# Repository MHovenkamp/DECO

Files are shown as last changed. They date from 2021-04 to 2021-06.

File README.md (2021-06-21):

# DECO

## Introduction

Welcome to the Github page for the social robot under 50 euros. This robot is the result of a student project by the name PINNO, personal innovation project. This robot is to be possibly used by the minor social robotics from Hogeschool Utrecht.

## What can the robot do?

DECO is a desk companion for people with a desk job. The robot reminds the user to stay healthy and productive without being pushy. The robot reminds people to take breaks and drink enough water. It can also inform the user of their current environment such as temperature. These are al possibilities within the robot but the goal is that this robot can easily be programmed by someone with limited knowledge of technology. THis is so the robot can be used by the previously mentioned minor from the HU.

## Printing the robot
Each part of the robot can be printed separated or if you have a bigger printer, be placed in one STL. Before you print you do have to add supports. This can be done easily with Ultimaker Cura.

## building the robot

The head:
The head consists of two parts: a roundish ball, the lower head and a dome for the face. 
1. Place the micro lidar and the oledscreen in the upper face and make sure that they are stuck using either a little bit of glue or some electricity tape.
2. place on of the servo motors in the g0 degree position, THsi can be done by connecting to the Arduino and running the return_to_start_pos command. Glue the neck horizontal to the servo motor making sure that there is a 90 degree angle between the motor and the neck.
3. place the servo with the neck part in the slot in the lower body and attach with some glue. 
4. Route all the cables for the components through the whole in the bottom of the lower body

The body:
1. Stick the servo through the bottom hole of the upper body. And turn the servo to 90 degrees. glue the vertical neck part to the servo with the attachment part diagonal to the servo. 
2. Attach the PIR sensor through the whole and attach with taper or glue. place the arduino in the bottom lower body and connect al the cables as shown in the Fritzing. 

Attachment
Connect the upper head to the lower head with some glue making sure the head looks up and down if the servo is moved. 
Slide the two neck pieces to each other attaching the robot together, make sure al the wires can get to the arduino with some space for movement. glue the lower and upper body together after connecting the usb cable into the arduino making sure the PIR sensor looks forward.

Voila! Robot. 

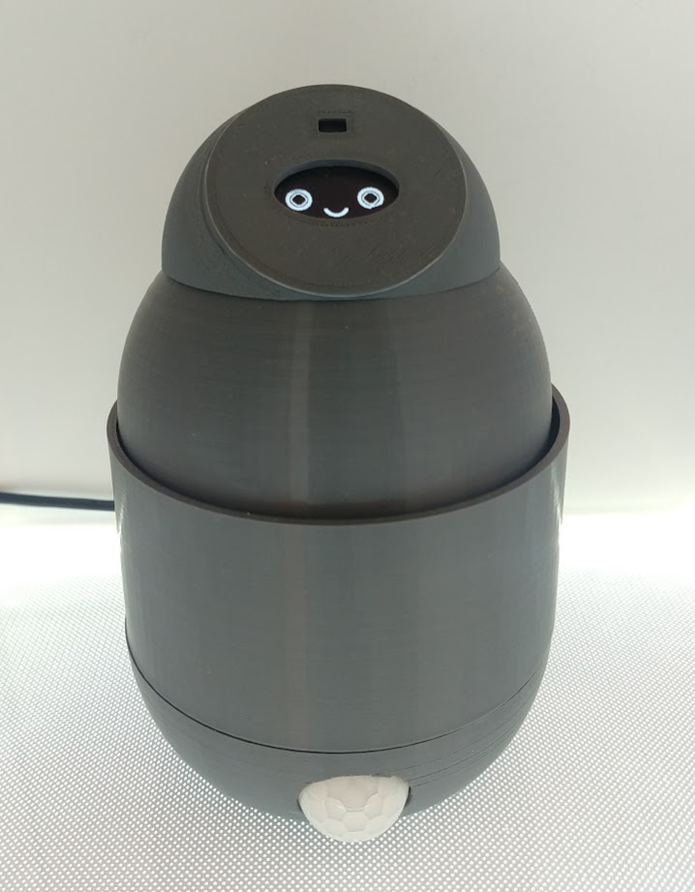
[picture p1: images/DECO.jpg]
DECO


## Necessary components to build this robot.

1. 3D printer
2. 2 * SG90 or SG92R servo motors, These both work the same but the SG92R ia a little stronger. 
    - [Amazon](https://www.amazon.nl/AZDelivery-Micro-Helikopter-Vliegtuigen-Inclusief/dp/B07CZ42862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)
3. Arduino nano 33 BLE SENSE
    - [Arduino store](https://store.arduino.cc/arduino-nano-33-ble-sense)
4. PIR sensor HC-SR501
    - [Amazon](https://www.amazon.nl/AZDelivery-HC-SR501-Detection-compatibel-Inclusief/dp/B07V6BY66P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)
5. OLED 0.96 display
    - [Amazon](https://www.amazon.nl/Jolicobo-OLED-weergavemodule-kijkhoek-doe-het-zelf-projectdisplay/dp/B07RNP3CMP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)
6. Piezo buzzer
    - [Amazon](https://www.amazon.nl/GLOGLOW-elektronische-zoemer-actieve-geluid/dp/B07F5LB8K9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)
6. Cables
    - Male to female 
    - female to female
7. Arduino compatible USB cable.
    - [Arduino store](https://store.arduino.cc/usb-cable-type-a-male-to-micro-type-b-male)
8. Soldering iron and necessary accessories.

total cost from amazon +- 63,18, You can probably get cheaper components from your local stores.  

## Documentation
For documentation run this command in the github directory
```
doxygen Doxyfile
```

## Models

### Fritzing
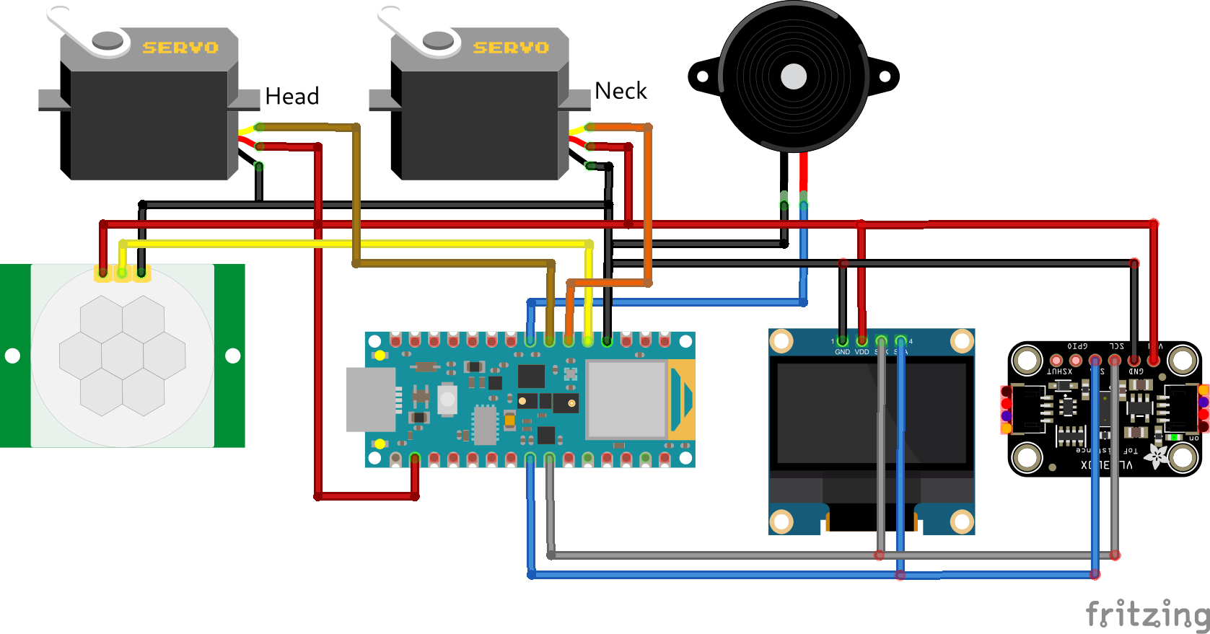
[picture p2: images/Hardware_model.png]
Fritzing Model


Al other models can be found by opening software_models.html.

## Building and running
This robot is compiled and flashed by [PlatformIO](https://platformio.org/). Install platformIO core to work with this project. Then run the following commands in a terminal in the directory. The directory will build the robot and flash to your arduino. PlatformIO will install all libraries and updates by itself. If something does not work try updating the libraries through platformIO trough the commando 
```
platformio update
```

To run: 
```
platformio run -t upload
```
If the right port cant be found change port to correct port with this command:
``` 
platformio run -t upload --upload-port <port>
```
You can find the correct port with:
```
pio device list
```
After flashing the robot will instantly start working. If the robot loses power and is then reconnected it will restart the program.

To open a serial monitor to the robot use the command:
```
pio device monitor
```

## Code layout
To write the preprogrammed code or to upload a file the code given has to be in a certain structure:

The setup wil run once and can be used to place som e setters before you start your program. The loop section will do exactly that: loop until the robot dies or power is removed.

```
SETUP:

// setup code

LOOP:

// code that will be looped

EOF:
// define end of code file

```

## command line interface
The command line interface has 3 ways to start code with.
1. REPL
2. FILE
3. PREPROGRAMMED FILE

### REPL 
You can enter a single command in here to see the result instantly. You can not test with integers since they are not saved from previous commands
### FILE
Ctrl+C plus Ctrl+V a full file in to the terminal to instantly parse and run the code. Warning: The serial buffer for arduino is famously unreliable so bigger files will most likely be read wrong. For files bigger then 10 lines of code use the PREPROGRAMMED FILE function.
### PREPROGRAMMED FILE
Start the preprogrammed file found in the programCode.cpp file. You have to recompile the robot every time you change this file. This file will also be played if no serial monitor is started.

## Commands:

### Instant commando's
- ```shutdown```, The robot shuts down until movement is detected.
- ```interactive_mode```, The robot tries to follow an object in front of its face but looses interest if no object is found.
- ```break_reminder```, Show the break reminder on the screen for the set duration. 
- ```walk_reminder```, Show the walk reminder on the screen for the set duration.
- ```water_reminder```. Show the water reminder on the screen for the set duration.
- ```show_weather_station```,show the weatherstation on the screen for the set duration. NOTE: The temperatures, BARO and humidity are measured inside the robot and can be inaccurate. 
- ```rng_movement```, move the robot once to a random position.
- ```return_to_start_pos```, Return the robot to the start position of 90 by 90 degrees. 
- ```move_head x```, move the head to x degrees. 40 <= x => 140
- ```move_neck x```, move the neck to x degrees. 0 <= x => 180.
- ```playSound x``` play start up sound. x:
    -   start_up
    -   shut_down
    -   notification
- ```WAIT x y```. x: Integer, y: cannot be an integer variable
    -   define HOUR 
    -   MINUTE 
    -   SECOND 
    -   MIllI_SECOND 

### IF conditions
You can maken if statement using some of the getters describe in the next paragraph. You can not place one if statement in another if statement. 
```
IF(getState = IDLE){
    // Code to execute if statement is true.
}
```
Possible commands:
-   getDistance >/</<=/>=/==/!= int
-   getState == STATE
-   getHeadPos >/</<=/>=/==/!= int
-   getNeckPos >/</<=/>=/==/!= int
-   getLastMovementDetected >/</<=/>=/==/!= int

you can use an int variable for every int mentioned above.

### WHILE loops
You can make a small part of your code loop for as long as a given condition is true
```
WHILE(getState = IDLE){
    // Code to loop execute if statement is true.
}
```
possible conditions1
-   x : X can be any number, The loop wil continue for x iterations.
-   getDistance >/</<=/>=/==/!= int
-   getState == STATE
-   getHeadPos >/</<=/>=/==/!= int
-   getNeckPos >/</<=/>=/==/!= int
-   getLastMovementDetected >/</<=/>=/==/!= int
IMPORTANT: if you change the value of an integer value used in the condition this change will not affect the x used in the condition. You can not use getHeadPos > x and then change x in the while loop to shorten or lengthen the loop. 

### Integers and math
The code for this robot contains a small amount of possible math. You can assign a number to a variable like this:
```
x = 6
variable = 6
variable_number = 6
```
You can add, subtract, divide and multiply with integers. You can only change existing integers.
```
SETUP:
    x = 2
    y = 3
    x + y # result = 5

    x = 2
    y = 3
    x - y # result = -1

    x = 2
    y = 3
    x * y # result = 6

    x = 6
    y = 3
    x / y # result = 2
EOF:
```
You can use numbers for the right side of any math operator
```
SETUP:
    x = 2
    x + 3  # result = 5

    x = 2
    x - 3 # result = -1

    x = 2
    x * 3 # result = 6

    x = 6
    x / 3 # result = 2
EOF:
```
limitations
You can not assign the output of a function to an integer variable.

### Getters
- ```getDistance```, Get the distance currently measured by head lidat
- ```getBreakTime```, Get the duration of the break time reminder.
- ```getWalkTime```. Get the duration of the walk time reminder.
- ```getWaterTime```, Get the duration of the water time reminder.
- ```getWeatherStationTime```, Get the duration of the weather station.
- ```getState```, get the current state of the robot:
    -   IDLE,
    -   REMINDER_BREAK
    -   REMINDER_WATER
    -   REMINDER_WALK
    -   WEATHER_STATION
    -   INTERACTIVE_MODE
    -   OFF
-   ```getHeadPos```, get the current position of the head in degrees with 90 being straight forward.
-   ```getNeckPos```, get the current position of the neck in degrees with 90 being straight forward.

### Setters
Set if timed functions are active or not:
- ```weatherstation = x```:
    -   ACTIVE
    -   NON_ACTIVE
- ```walk_reminder = x```:
    -   ACTIVE
    -   NON_ACTIVE
- ```weatherstation = x```:
    -   ACTIVE
    -   NON_ACTIVE
- ```break_reminder = x```:
    -   ACTIVE
    -   NON_ACTIVE
Set the state of the robot
- ```STATE = x```:
    -   IDLE,
    -   REMINDER_BREAK
    -   REMINDER_WATER
    -   REMINDER_WALK
    -   WEATHER_STATION
    -   INTERACTIVE_MODE
    -   OFF
Set the time duration after which the robot will shut down if there is no movement.
- ```shut_down_after = x y```: x = integer, y = 
    -   HOUR 
    -   MINUTE 
    -   SECOND 
    -   MIllI_SECOND 
set the duration and the period of a timed event.
a :
-   weatherstation
-   walk_reminder
-   water_reminder
-   break_reminder
- ```a DURATION = x y```: x = integer, y = 
    -   HOUR 
    -   MINUTE 
    -   SECOND 
    -   MIllI_SECOND 
- ```a PERIOD = 10 MINUTE```: x = integer, y = 
    -   HOUR 
    -   MINUTE 
    -   SECOND 
    -   MIllI_SECOND 
set how long the robot i allowed to follow an object in interactive mode.
- ```interactive_mode DURATION = x y```: x = integer, y = 
    -   HOUR 
    -   MINUTE 
    -   SECOND 
    -   MIllI_SECOND 

## License 

DECO
Copyright (C) <year>  <name of author>

This program is free software: you can redistribute it and/or modify
it under the terms of the GNU General Public License as published by
the Free Software Foundation, either version 3 of the License, or
(at your option) any later version.

This program is distributed in the hope that it will be useful,
but WITHOUT ANY WARRANTY; without even the implied warranty of
MERCHANTABILITY or FITNESS FOR A PARTICULAR PURPOSE.  See the
GNU General Public License for more details.

You should have received a copy of the GNU General Public License
along with this program.  If not, see <https://www.gnu.org/licenses/>.

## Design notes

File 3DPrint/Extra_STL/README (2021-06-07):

Some people had issues printing the upper body of the robot. Therefore two new STL files have been made to make it possible to print the upperbody in two seperate pieces. The upper body can now be connected to the middle body to form the original upper body.

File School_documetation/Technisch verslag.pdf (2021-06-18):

## Maaike Hovenkamp

1741256

# DECO Technisch verslag

18-06-2021

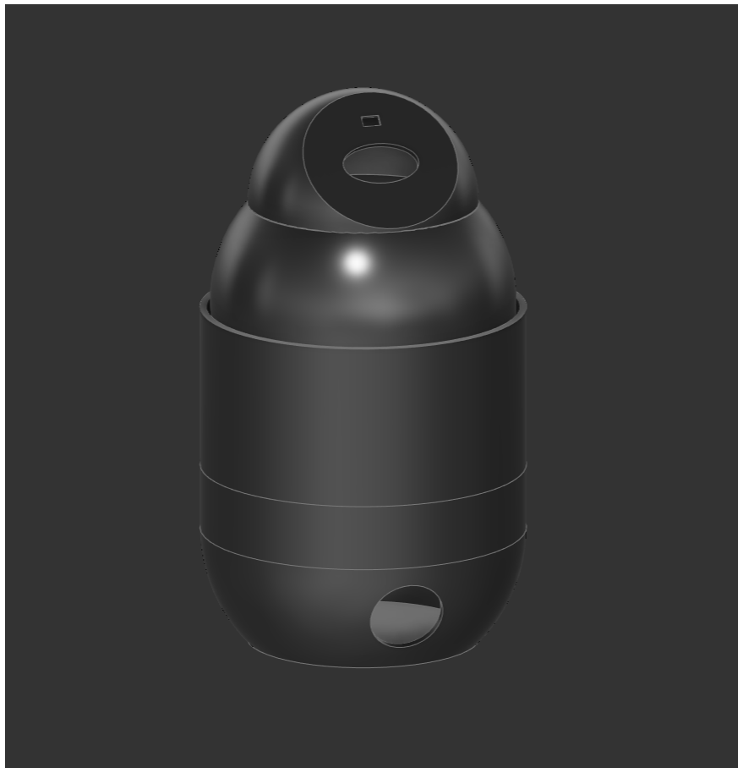
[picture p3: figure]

Inleiding | 2
Microcontroller | 2
Ontwikkelings taal | 2
Python | 3
C++ | 3
Ontwikkelingsomgeving | 3
Resultaten software | 4
Externe hardware | 4
Servomotoren | 4
Externe Sensoren | 4
Display | 4
Bronnen | 5

## Inleiding

Dit is het technisch verslag voor de DECO robot, er wordt ingegaan op de specifieke gekozen hardware en ontwikkel omgeving. Er wordt niet ingegaan op het fysieke ontwerp van de robot aangezien dit is opgenomen in het Design verslag.

## Microcontroller

Het hart van de robot is de microcontroller die het hele systeem laat werken. Voor deze robot is er gekozen voor de Arduino nano 33 BLE SENSE. Deze arduino is gekozen voor zijn snelheid en kleine vorm.

De arduino nano is een microcontroller van het merk Arduino en werkt op een nRF52840 processor van Nordic Semiconductors. Deze microcontroller heeft meer geheugen en ram dan de grotere arduino Uno. waardoor er grotere programma’s kunnen worden geschreven.

De nano 33 ble sense is een uitbreiding op de arduino nano 33 ble en komt met extra sensoren die gebruikt kunnen worden om kennis van de omgeving te verzamelen.

## Ontwikkelings taal

De gekozen microcontroller is een relatief nieuwe microcontroller, 2019, waardoor er bepaalde limieten zijn in keuze van ontwikkelings talen. Er zijn twee taal mogelijkheden voor deze microcontroller: een vorm van Python en C++.

## Python

Python is een redelijk toegankelijke taal voor de beginnende programmeur waardoor gebruikers op een dieper niveau met de robot kunnen werken. Python zelf werkt niet op microcontrollers maar er zijn aanpassingen op python gemaakt zodat het bruikbaar is op een microcontroller. Circuitpython van Adafruit is er hier een van. Het is een verdere uitbouw op MicroPython. Circuitpython heeft een eigen bootloader die eerst op de arduino moet worden geïnstalleerd. Momenteel is er geen Circuit Python implementatie voor de arduino nano 33 ble sense maar wel voor zijn lite versie de arduino nano 33 ble. Deze lite versie heeft minder sensoren dan de arduino nano 33 ble sense waardoor veel sensoren van de arduino nano 33 ble sense niet ondersteund worden door circuit python. De sensoren op de arduino nano 33 ble sense hebben zelf libraries van circuit python maar hier wordt gewerkt met externe sensoren. Een voordeel van circuit python is de geïntegreerde REPL waardoor code snel kan worden getest. Dit heeft een voordeel voor de gebruiker als deze gebruiker niet bekend is met het schrijven van code.

C++

De makers van de arduino nano 33 ble sense maken zelf ook de libraries en andere support voor hun producten. Deze libraries zijn geschreven en bedoeld voor de taal C++. C++ is een moeilijkere taal dan python gefocust op snelheid. Aangezien de makers van de arduino zelf hun libraries maken is er volledige support voor de arduino nano 33 ble sense. Er zijn libraries ontwikkeld voor alle sensoren en deze worden ook regelmatig geupdate. Een belangrijk punt van C++ en arduino is dat alle code op de laptop gecompileerd wordt voordat het naar de arduino wordt gestuurd. Dit zorgt ervoor dat alle code moet bestaan voordat de gebruiker kan testen en heeft een bepaalde wachttijd.

Er is voor dit project gekozen om en de taal C++ te werken aangezien de support van de makers betrouwbaar en constant is. Dit zorgt er wel voor dat er voor de user interface mogelijk niet met REPL kan werken. Dit zou betekenen dat er een langere wachttijd is voor de gebruiker.

## Ontwikkelingsomgeving

Met de keuze voor C++ zijn er ook een aantal mogelijke ontwikkelomgevingen geopend. Arduino heeft een standaard ontwikkelomgeving waar code geschreven, gecompileerd en geflashed kan worden. Het nadeel van deze omgeving is dat er weinig debug opties zijn en dat er geen bestanden naast elkaar open kunnen worden gezet. Zelf heb ik een voorkeur voor visual studio code door zijn vele debug opties en nette interface. Er is de mogelijkheid op de arduino IDE bestanden te openen en te bewerken met visual studio code maar ze zouden alsnog met de arduino IDE gecompileerd en geflashed moeten worden. Om deze redenen ben ik overgestapt op Platformio. PlatformIO is een een cross platform visual studio code extensie waarmee code voor microcontrollers kan worden geschreven in C++ met alle arduino libraries (PlatformIO labs, n.d.). Alle code wordt geschreven, gecompileerd en geflashed met behulp van PlatformIO zonder dat de arduino IDE gebruikt wordt. Om alleen code te compileren en te flashen is er ook cross platform command line support.

## Resultaten software

De uiteindelijke keuzes voor dit project zijn:

Het DECO project wordt in de taal C++ geschreven voor de arduino nano 33 ble sense en gecompileerd een geflashed door PlatformIO.

## Externe hardware

Om ervoor te zorgen dat de robot met zijn omgeving kan interacteren wordt er gebruik gemaakt van externe hardware.

## Servomotoren

Om de robot te laten bewegen zijn er twee servomotoren aan het ontwerp toegevoegd. Er is gekozen voor de sg92R. Dit is een kleine compacte servomotor met genoeg kracht om de robot te laten bewegen zonder een externe voedingsbron te hebben (ServoDatabase, n.d.).

## Externe Sensoren

De robot heeft buiten de microcontroller ook een paar externe sensoren. Een van deze sensoren is een Passive Infrared sensor, PIR, DIe opmerkt of er beweging in de ruimte is. DIt wordt gebruikt om te testen of de robot niet alleen in een ruimte is. De HC-sr501 is een adequate sensor voor deze situatie met een degelijk bereik (MPJA, n.d.). Om een persoon te detecteren binnen een ruimte maakt de robot gebruik van een tweede sensor geplaatst in het hoofd. Dit is de sensor vl53l0x. Deze kleine afstand sensor is goed te verwerken in het ontwerp is precies genoeg. (Tinytronics, n.d.)

## Display

Er wordt gebruikgemaakt van een zwart wit I2C display ter grootte van 128*64 pixels. Dit is een kleine maar efficiënte display met een laag stroomverbruik (Adafruit).

## Bronnen

Adafruit. (2008, April). SSD1306 Datasheet. cdn-shop.adafruit.com. Retrieved 6 15, 2021, from

https://cdn-shop.adafruit.com/datasheets/SSD1306.pdf

MPJA. (n.d.). HC-sr501 datasheet. MPJA. https://www.mpja.com/download/31227sc.pdf

PlatformIO labs. (n.d.). PlatformIO. platformio.org. Retrieved 6 16, 2021, from https://platformio.org/

ServoDatabase. (n.d.). SG92R datasheet. ServoDatabase.com.

https://servodatabase.com/servo/towerpro/sg92r

Tinytronics. (n.d.). Tinytronics, datasheet link. TinyTronics.

https://www.tinytronics.nl/shop/nl/sensoren/afstand/vl53l0x-time-of-flight-tof-afstandsenso

r

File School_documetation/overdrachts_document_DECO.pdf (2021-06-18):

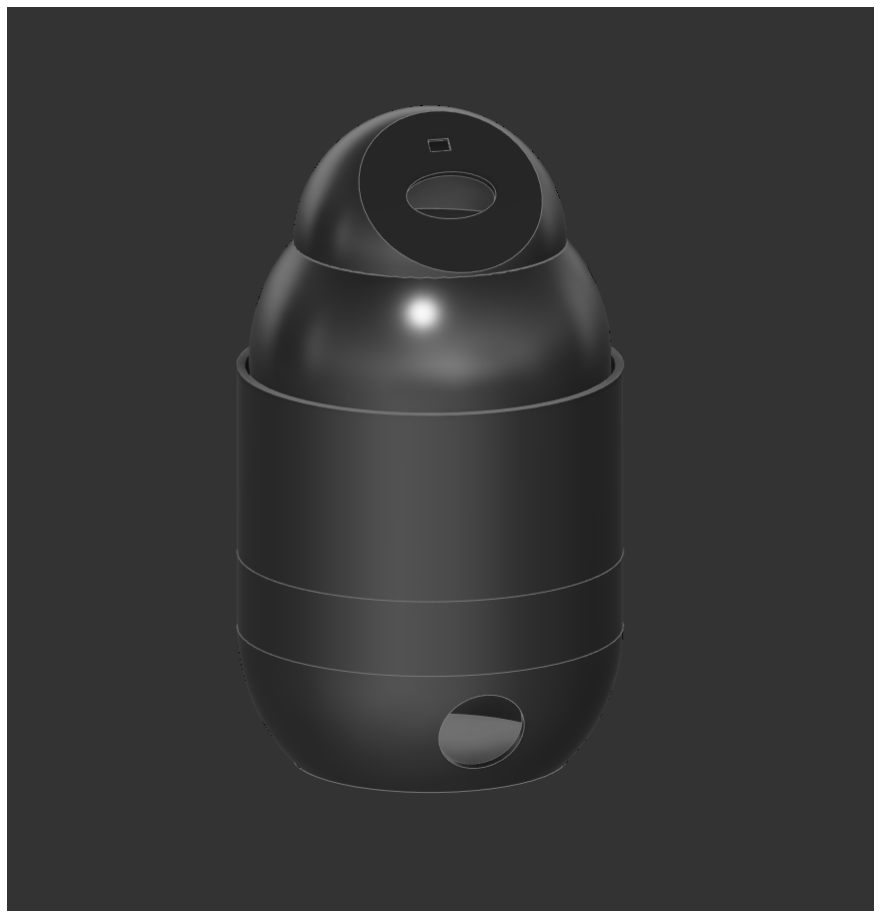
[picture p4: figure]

# Overdrachtsdocument DECO

18-06-2021
─

## Maaike Hovenkamp

### Personal innovation 2021

## Inleiding

Welkom bij de inleiding voor het overdrachtsdocument voor de sociale desktop companion DECO. DECO is een makkelijk programmeerbare robot voor op je bureau om je gezelschap te houden door de dag heen. DECO kan gebruikt worden om je te herinneren voor jezelf te zorgen door de dag heen en je te vermaken met een klein spelletje. Om ervoor te zorgen dat de robot makkelijk toegankelijk is, is er gekozen voor goedkopere onderdelen. Met amazon komt het totaal uit op +- 64 dollar maar lokale bronnen hebben vaak goedkopere onderdelen.
DECO is volledig ontworpen en geproduceerd door Maaike Hovenkamp.
Inleiding | 1
Artefacten | 1
STL files voor DECO | 1
Software | 2
Software & hardware modellen | 2
Documentatie | 2
Bugs en beperkingen | 3
Bugs | 3
Beperkingen | 3
Product backlog | 3

## Artefacten

Alle documentatie is te vinden op de Github pagina: https://github.com/MHovenkamp/DECO

## STL files voor DECO

Om de robot te printen zijn zes STL files geproduceerd:
1. Neck horizontal part, Deel 1 van neck gedeelte.
2. Neck vertical part, Deel 2 van neck gedeelte.
3. Lower body, voet van de robot met gat voor voeding en PIR-sensor
4. Upper body, Verlengstuk voor de voet met kom voor hoofd.
5. Lower head, bodem van hoofd passend in de kom van het lichaam.

6. upper head, Hoofd met gat voor OLED-screen en LIDAR module.

Er is een extra set aan STL file voor de upper body waarin dit onderdeel in 2 stukken is gesneden.

## Software

Om de robot te besturen is er code geschreven in C++ op het framework van PlatformIO. PlatformIO is een cross-platform embedded development platform integreerbaar in visual studio code. De robot maakt gebruik van een paar libraries:
1. Adafruit BusIO, Oled screen
2. Adafruit GFX Library, Oled screen
3. Adafruit SSD1306, Oled screen
4. Adafruit_VL53L0X, LIDAR
5. Arduino_HTS221, interne luchtvochtigheid en temperatuur
6. Arduino_LPS22HB, interne BARO sensor
Om met de software te werken moet PlatformIO geïnstalleerd worden en de github pagina als project ingeladen worden. Alle libraries en build platformen worden automatisch geïnstalleerd bij de eerste build.

## Software & hardware modellen

Voor de software zijn modellen gemaakt volgens de UML methode:
1. Object model
2. Task scheduling
3. Class diagram
4. State transition diagrams.
Er is een fritzing voor de kabel layout.
Deze bestanden zijn te vinden op de Github pagina.

## Documentatie

Voor de DECO robot zijn verschillende verslagen geschreven.
1. Design document, Een overzicht van alle design keuzes en de daaruit volgende Use cases. In dit verslag zijn de keuzes voor hardware en software niet vastgelegd.
2. Technische verslag, In dit verslag wordt er een onderbouwde keuze gemaakt voor:
a. Code taal
b. Ontwikkelomgeving
c. Hardware

## Bugs en beperkingen

Na vier maanden werken aan de DECO robot zijn de volgende bugs en beperkingen aanwezig:

### Bugs

- De robot heeft momenteel een probleem met een tikkend geluid over de I2C bus. Een tik is hoorbaar.
- De robot verliest af en toe de functionaliteit over de servo motoren. Na de een keer de kabels te hebben bewogen werkt de robot weer. De kans dat het een slechte kabel is bestaat maar het kan ook een probleem zijn met de stroomlevering. Het probleem wordt significant minder als de servomotoren geen ground meer delen met het Oled scherm.
- De serial input van Arduino is niet extreem betrouwbaar waardoor file input vanaf de terminal na een bepaalde grootte niet meer succesvol werkt.

### Beperkingen

- De robot heeft momenteel 6 threads lopen waardoor een getimede task later kan zijn. Een interpreter commando kan een seconde achterlopen. Alle sensoren worden wel correct getimed.
- De codetaal is momenteel erg beperkt. Momenteel worden een aantal robot commandos ondersteunt en een hele minimale interpreter met integer support, if nodes en while nodes. Alles wordt geparsed en gelexed maar er kunnen meer specifieke errors worden toegevoegd en betrouwbaarheid kan hoger. DIt kan gedaan worden door bijvoorbeeld elk commando met een ; af te sluiten en hier op te parsen.

## Product backlog

Hierbij de originele use cases, een volledig overzicht is te vinden in het design document.
1. Als gebruiker wil ik dat de robot mensen herinnert om elk half uur minimaal vijf minuten te bewegen.
2. Als gebruiker wil ik dat de robot mensen herinnert om elke twee uur een pauze te nemen.
3. Als gebruiker wil ik dat de robot mensen herinnert om elk uur een glas water te drinken.
4. Als gebruiker wil ik dat de robot een uitknop heeft waar de robot mee uitgeschakeld kan worden.

5. Als gebruiker wil ik dat de robot gebruik maakt van piepjes, beweging en afbeeldingen om te communiceren.
6. Als gebruiker wil ik dat de robot heeft een scherm waarop instructies kunnen worden getoond.
7. Als gebruiker wil ik dat alle documentatie rond het gebruik van de robot in engels wordt geschreven.
8. Als gebruiker wil ik dat de robot op een standaard USB-poort kan worden aangesloten voor stroom.
9. Als gebruiker wil ik dat de robot geen gegevens deelt met derde partijen.
10. Als gebruiker wil ik dat de robot geen gegevens over de gebruiker verzamelt afgezien van wat de gebruiker de robot geeft.
11. Als gebruiker wil ik dat de robot geen scherpe randen of puntige objecten heeft.
12. Als gebruiker wil ik dat de robot stationair is en niet zonder de hulp kan verplaatsen.
13. Als gebruiker wil ik dat de robot de vooraf geplande acties uitvoert en hier niet van afwijkt.

De enige use case die niet uitgewerkt is een mogelijke uitknop voor de robot.
De originele backlog voor dit ontwerp is grotendeels afgerond maar ik wil in dit kopje wat verdere inspiratie geven voor mogelijke toekomstplannen voor DECO.
Verdere interpreter mogelijkheden:
1. Toevoegen van een printfunctie voor debuggen. Outputen van integer waarden en string variabelen.
2. Output van functies opvangen in integer nodes en hiermee kunnen rekenen.
3. Implementeren van bolean waardes, momenteel kunnen integer nodes hiervoor gebruikt worden maar een individuele variabele soort kan gewaardeerd worden. Robot mogelijkheden
1. Meer vormen van interactie met de gebruiker, denk aan meer vormen van geluid.
2. De microcontroller van de robot kan een klein tensorflow model ondersteunen, De robot kan meer sociaal worden als hij zelf meer keuzes kan maken. Met een klein neuraal netwerk zouden meer natuurlijke keuzes kunnen worden gemaakt.

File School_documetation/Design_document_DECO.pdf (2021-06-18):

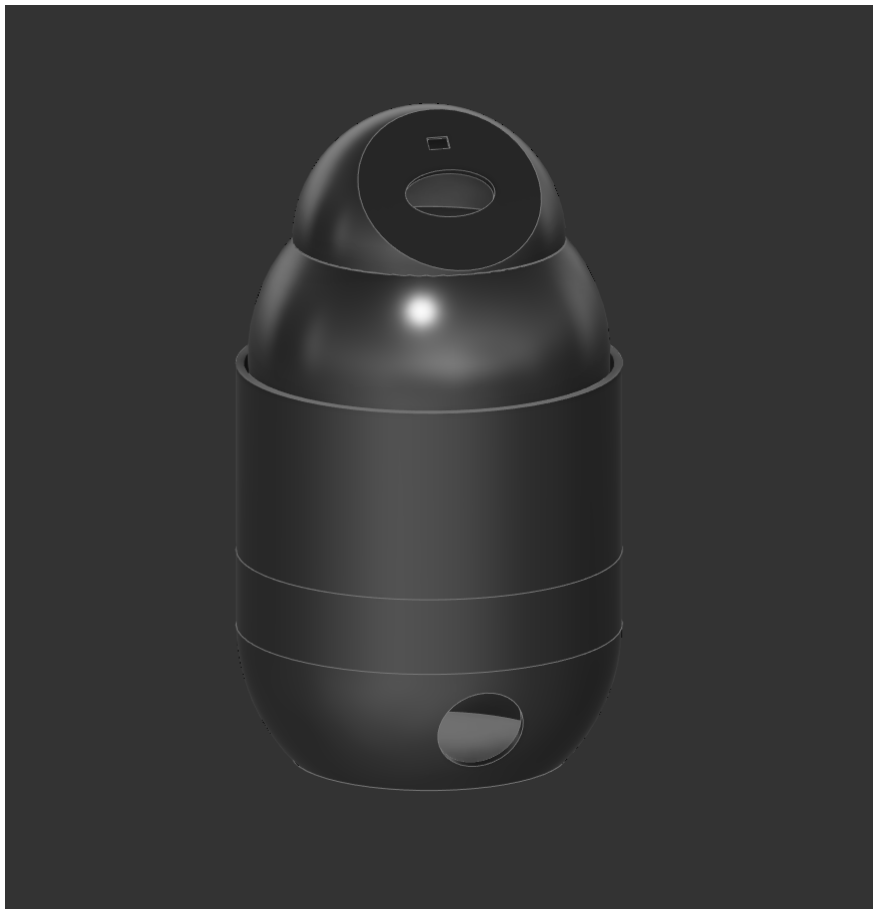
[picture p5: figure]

# Design document DECO

18-6-2021

## Maaike Hovenkamp

### Personal Innovation Hogeschool Utrecht

1741256

## Overzicht

Dit is het ontwerp document voor het Personal Innovation project van Maaike Hovenkamp. In dit document ga ik mijn ontwerpprocess uitwerken en uitleggen.

Als eerste ga ik over een paar verschillende bestaande robots om te kijken of deze robots sociaal zijn en om te kijken of ik deze robots als basis kan gebruiken voor mijn robot. Hierna ga ik op deze robot verderwerken met onderstaande methoden of begin ik een volledig nieuw ontwerpprocess.

Ik ga verschillende methoden van de minors “Design methods for robots” en “Human robot interaction” toepassen. Met deze methoden hoop ik een goed ontwerp te maken om daarmee een succesvolle sociale robot te maken.

Het doel van mijn sociale robot wordt om een desk companion te zijn en om lange werkdagen leuker te maken. De robot kan op een bureau geplaats worden en zorgd voor interactie met de gebruiker wat eenzaamheid verminderd. De robot zal ook een paar nuttige functies krijgen om de gebruiker te helpen bij self care. Deze functies zullen uit een value sensitive design process komen.

Als er een robot ontwerp gemaakt is zal ik de robot naast een framework leggen om te kijken of de robot als “sociaal” kan worden beschreven. Dit framework is gemaakt door Christoph Bartneck en Jodi Forlizzi (Bartneck & Forlizzi, 2004, 591-594).

In dit bestand worden een aantal termen gebruikt uit de twee vakken van de minor Social Robotics. Veel van deze termen worden gebruikt in opsommingen. Als de betekenis van de termen voor de lezer belangrijk is zullen deze worden uitgelegd. Als de termen niet uitgelegd zijn betekent dit dat er niet van de lezer verwacht wordt deze termen te begrijpen en staan zij erin voor tekst compleetheid.

Overzicht | 2
Bestaande robots | 4
Keuze fysieke ontwerprichting | 5
Value sensitive design | 6
Stap 1, Value discovery | 6
Directe stakeholders | 6
Indirecte stakeholders | 6
resultaten | 6
Stap 2, Value conceptualization | 8
Human welfare | 9
Privacy | 9
Universal usability | 10
Trust | 10
Autonomy | 11
Stap 3, Empirical value investigation & Stap 4, Technical value investigation | 11
Human welfare | 12
Privacy | 12
Universal usability | 13
Trust | 13
Autonomy | 14
Use cases | 15
MoSCoW | 21
Robot ontwerp | 21
Gezicht animaties | 23
Robot naamgeving | 25
Bronnen | 25

## Bestaande robots

Er is gekeken naar 11 verschillende robots om te kijken of dit een robot is om verder op te ontwikkelen of om als inspiratie te nemen. De onderzochte robots zijn:

❏ Buddy
❏ Tito
❏ The emotion robot
❏ littlebot
❏ peeqo

❏ vector
❏ pia
❏ pico
❏ emo

Deze robots zijn beoordeeld op hoe sociaal ze zijn met het framework van Christoph Bartneck en Jodi Forlizzi (Bartneck & Forlizzi, 2004, 591-594). Binnen dit framework krijgen robots een score op 5 verschillende gebieden:

- Form, Is de robot abstract, biomorphic or anthropomorphic? verdere uitleg in volgend kopje.
- Modality, Is de robot unimodal or multimodal? heeft de robot meerdere vormen van interactie: zoals beweging en geluid.
- Social norms, Heeft de robot begrip van sociale normen?
- Autonomy, Beslist de robot zelf welke acties worden uitgevoerd?
- Interactivity, Is er de mogelijkheid om met de robot te interacteren?

Op basis van dit framework heb ik de robots een sociale score gegeven om ze te kunnen ordenen. Ik heb opgeschreven welke design keuzes ik zou willen meenemen van de robots en of ik de robots zou kunnen reproduceren in de tijd voor dit project, 2 schoolblokken +- 4 maanden. Hieronder een overzicht van elke score. De bronnen van de robots kunnen aan het eind van dit bestand gevonden worden.

naam robot | Sociale score 1/10 | mogelijkheid om te maken | Wat wil ik meenemen uit dit design
Buddy | 5 | ja | De Buddy robot is een goed na te maken robot en heeft veel ruimte voor verbetering. Ik vind de beweging van de nek interessant en neem dit waarschijnlijk mee naar mijn eigen ontwerp.
Tito | 3 | ja | De Tito robot heeft niet veel wat ik mee zou willen nemen. Misschien de interactie van het dansen.
The emotion robot | 1 | nee | Het design is schattig en ik wil het scherm gezicht idee overnemen in mijn eigen ontwerp.

Littlebot | 2 | nee | Van de Littlebot wil ik niet iets meenemen.
Vector | 9 | nee | Van de Vector wil ik de nuttige functies overnemen zoals een mogelijk weerstation of een herinnering om wat te drinken en een rondje te lopen.
PIA | 6 | nee | Van de PIA robot wil ik mogelijk het oogcontact overnemen
Pico | 8 | nee | van de Pico robot wil ik niks overnemen
Emo | 10 | nee | Van deze robot wil ik het sociale aspect overnemen. De robot is meer voor plezier dan voor een nuttig doel.
Peeqo | 9 | nee | Van Peeqo wil ik niks overnemen.

Zoals te zien is de hoogst scorende robot die ik zou kunnen maken de Buddy robot. Deze robot heeft maar een sociale score van 5 en is daarmee niet erg sociaal. De robot geeft de indruk dat de robot menselijk gedrag snapt en hierop reageert maar dat is niet wat er echt gebeurd. De robot beweegt in een willekeurig patroon en “kijkt” af en toe naar een object. Om deze redenen kan de robot niet als een echte sociale robot worden gezien.

De Buddy robot is wel de soort robot die ik als inspiratiebron wil meenemen. De werking van de nek en de mogelijkheden om rond te kijken waren het sociaalste aspect van de robot en zijn goed te implementeren.

Robots met een hogere score dan 5 zijn professionele robots gemaakt door bedrijven in teamverband. Deze robots zijn niet geschikt voor ontwikkeling in een kortere tijdsperiode.

## Keuze fysieke ontwerprichting

Er zijn verschillende vormen van robots binnen het sociale robot gebied. Er zijn anthropomorphic, zoomorphic, karikatuur en functioneel. Anthropomorphic is een robot met menselijke eigenschappen en zoomorphic met dierlijke eigenschappen. Karikatuur is het standaard beeld van mensen over robots geinspireerd door bijvoorbeelde de Disney film Wally. Functioneel is puur technisch en er is weinig gedaan aan het uiterlijk van de robot, alle motoren en sensoren zijn te zien.

Mijn keuze is voor een karikatuur robot. Ik kies voor deze ontwerp vorm aangezien deze vorm geen kans op uncanny valley heeft, het effect waarbij menselijke robots als eng worden beschouwd omdat ze net niet menselijk genoeg zijn en dus niet “kloppen”. Deze ontwerpkeuze is ook gemaakt voor de Buddy robot welke ik neem als inspiratiebron. Ik wil mijn robot wel menselijke trekken geven om emotie mee te tonen. Ik wil deze mogelijkheden wel simpel houden. De menselijke trekken die ik aan mijn robot wil toevoegen gaan komen uit een value sensitive design process. uit dit process komt ook alle functionaliteit die ik mijn robot wil geven.

Als startvorm wordt de ronde voet van de Buddy robot meegenomen en het concept dat de robot rond kan kijken met een hoofd.

## Value sensitive design

Met value sensitive design wordt een robot ontworpen vanuit menselijke waarden. Dit kunnen waarden als vertrouwen en vrijheid zijn. Door deze waarden als uitgangspunt te nemen wordt de robot sneller door gebruikers geaccepteerd in een persoonlijke omgeving.

## Stap 1, Value discovery

De eerste stap van value sensitive design is bepalen welke menselijke waarden het systeem moet vertegenwoordigen. Deze waarden worden bepaald door de stakeholders van het systeem.

### Directe stakeholders

- De gebruiker van de robot, De doelgroep van de robot is voor werkende mensen met een bureaubaan van 12 tot 65 jaar oud. Deze groep mensen is de groep mensen die op een dag de meeste uren stilzitten (Rijksinstituut voor Volksgezondheid en Milieu, 2018).

### Indirecte stakeholders

- De maker van het product. Als maker van het product worden mijn normen en waarden onbewust in het ontwerp verwerkt. Dit is bewezen in de studie (Cheon & Makoto Su, n.d.,)
- Opdrachtgevers, In dit geval Personal Innovation begeleider Wouter van Ooijen.

Nu de directe en indirecte stakeholders zijn vastgesteld wordt aan de directe stakeholders hun waarden gevraagd. Dit kan gedaan worden met meerdere methoden. Er is gekozen voor een vragenlijst die beantwoordt wordt door een groep indirecte stakeholders. Deze vragenlijst bestaat uit een aantal open en gesloten vragen waaruit de values van de directe stakeholders naar voren komen. Deze vragenlijst zal in de vorm van een Google Form worden verstuurd.

### Resultaten

In totaal hebben 10 mensen uit de indirecte stakeholders groep hun mening gegeven over menselijke waarden die ze zouden willen terugzien. De leeftijden van de test groep reikt van 16 tot 52. Van de 5 vragen is vraag 3 het belangrijkst. Hier wordt aan de stakeholders gevraagd welke 3 menselijke waarden uit de lijst menselijke waarden van Friedman en Henry voor hen het belangrijkst is. Ook is vraag 5 interessant waarin wordt gevraagd welke menselijke waarde in elk design, niet alleen robots, zou moeten voorkomen. De overige vragen zijn open vragen om een beter beeld te krijgen van het beeld van de stakeholder.

Alle 5 vragen::

1. Als jij aan een sociale companion robot denkt, wat zie jij dan voor je? Benoem het uiterlijk van de robot en een paar mogelijke functionaliteiten.
2. Wat zijn voor jou terughoudende factoren in het gebruik van een sociale robot? Als je geen terughoudingen hebt kun je deze vraag overslaan.
3. Welke drie menselijke waarden vind jij het belangrijkst uit onderstaande lijst?
4. Wat vindt jij het lastigst aan lang aan een bureau werken? Wat vergeet je te doen of begint na een lange tijd te storen?
5. Wat is een menselijke waarde die jij in elk design zou willen terugzien? Dus niet alleen robots.

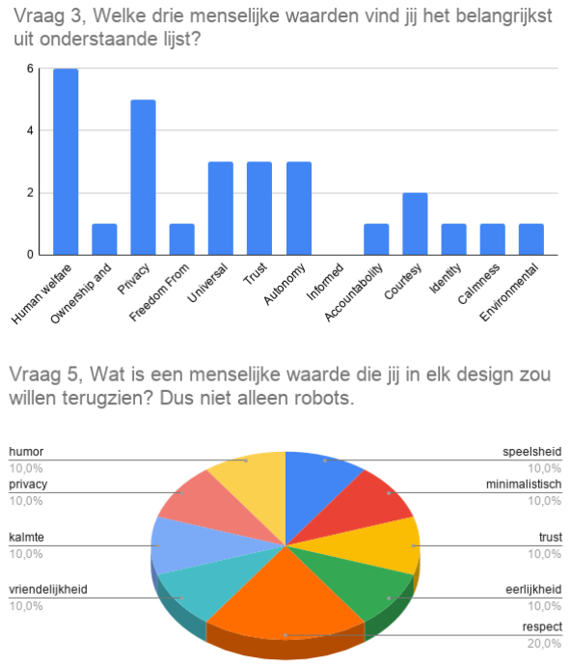
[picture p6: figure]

Voor verdere analyse ga ik de top 5 gekozen waarden verwerken, dit zijn:

1. Human welfare
2. Privacy
3. Universal
4. Trust
5. Autonomy

## Stap 2, Value Conceptualization

Nadat de stakeholders hun menselijke waarden hebben doorgegeven worden deze waarden opgesplitst in normen. Denk hierbij als voorbeeld aan de waarde: Dieren in gevangenschap moeten genoeg leefruimte hebben. Hieruit kunnen de normen komen: Elk dier moet 3 maal zijn lichaamslengte aan ruimte hebben en elk dier moet zich in een kooi kunnen uitstrekken om te liggen. Uit deze normen kunnen dan ontwerpelementen worden gehaald.

Ook wordt in deze fase gekeken op welke punten waarden elkaar kunnen tegenspreken of uitsluiten.

### Human welfare

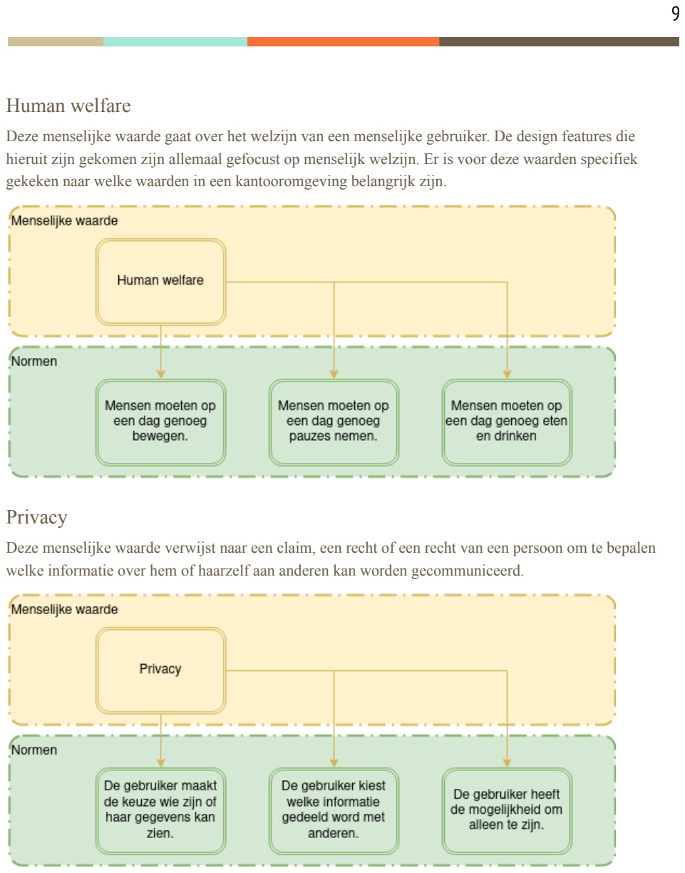
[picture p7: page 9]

Deze menselijke waarde gaat over het welzijn van een menselijke gebruiker. De design features die hieruit zijn gekomen zijn allemaal gefocust op menselijk welzijn. Er is voor deze waarden specifiek gekeken naar welke waarden in een kantooromgeving belangrijk zijn.

### Privacy

Deze menselijke waarde verwijst naar een claim, een recht of een recht van een persoon om te bepalen welke informatie over hem of haarzelf aan anderen kan worden gecommuniceerd.

### Universal usability

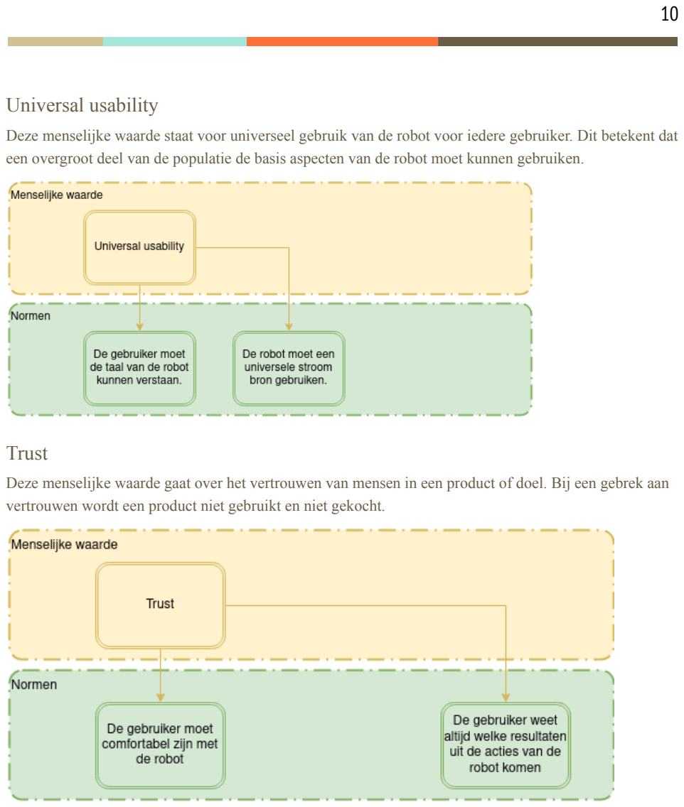
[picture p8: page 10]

Deze menselijke waarde staat voor universeel gebruik van de robot voor iedere gebruiker. Dit betekent dat een overgroot deel van de populatie de basis aspecten van de robot moet kunnen gebruiken.

### Trust

Deze menselijke waarde gaat over het vertrouwen van mensen in een product of doel. Bij een gebrek aan vertrouwen wordt een product niet gebruikt en niet gekocht.

### Autonomy

Deze menselijke waarde verwijst naar het vermogen van mensen om te beslissen, plannen en handelen op manieren waarvan zij denken dat ze het zal helpen hun doelen te bereiken.

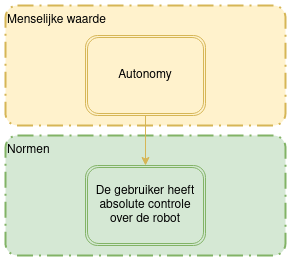
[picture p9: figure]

## Stap 3, Empirical value investigation & Stap 4, Technical value investigation

Aangezien ik value sensitive design gebruik om een nieuw robot design te maken in plaats van het verbeteren van een bestaand design zijn stap 3 en 4 in elkaar opgegaan. In deze stappen worden de menselijke waarden geprioriteerd en omgezet in design aspecten. Wat ik heb gedaan is eerst omzetten naar design aspecten en deze daarna prioriteren aangezien niet elke norm uit een menselijke waarde even belangrijk is. Als eerst zijn alle waarden omgezet in design features en deze worden daarna omgezet naar use cases. Deze use cases worden daarna geprioriteerd met de MoSCoW methode.

### Human welfare

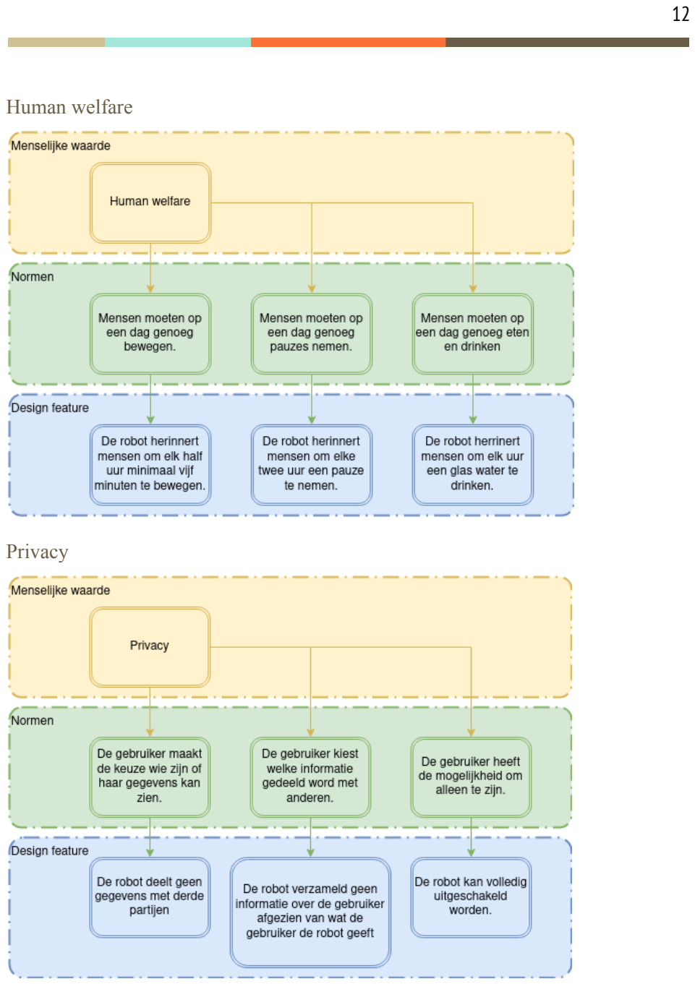
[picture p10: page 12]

### Privacy

### Universal usability

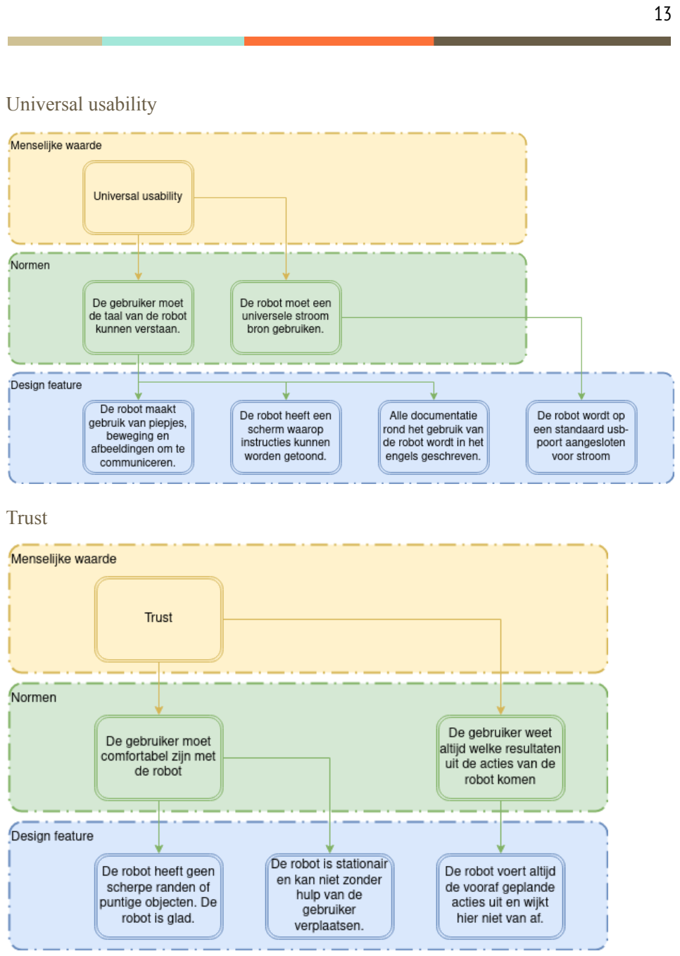
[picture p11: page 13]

### Trust

### Autonomy

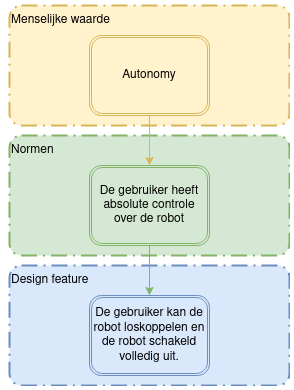
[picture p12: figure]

De designkeuzes die tot nu toe uit value sensitive sensitive design gekomen zijn, zijn:

1. Als gebruiker wil ik dat de robot mensen herinnert om elk half uur minimaal 5 minuten te bewegen.
2. Als gebruiker wil ik dat de robot mensen herinnert om elke 2 uur een pauze te nemen.
3. Als gebruiker wil ik dat de robot mensen herinnert om elk uur een glas water te drinken.
4. Als gebruiker wil ik dat de robot een uitknop heeft waar de robot mee uitgeschakeld kan worden.
5. Als gebruiker wil ik dat de robot gebruik maakt van piepjes, beweging en afbeeldingen om te communiceren.
6. Als gebruiker wil ik dat de robot heeft een scherm waarop instructies kunnen worden getoond.
7. Als gebruiker wil ik dat alle documentatie rond het gebruik van de robot in engels wordt geschreven.
8. Als gebruiker wil ik dat de robot op een standaard USB-poort kan worden aangesloten voor stroom.
9. Als gebruiker wil ik dat de robot geen gegevens deelt met derde partijen.
10. Als gebruiker wil ik dat de robot geen gegevens over de gebruiker verzamelt afgezien van wat de gebruiker de robot geeft.
11. Als gebruiker wil ik dat de robot volledig uitgeschakeld kan worden.
12. Als gebruiker wil ik dat de robot geen scherpe randen of puntige objecten heeft.
13. Als gebruiker wil ik dat de robot stationair is en niet zonder de hulp kan verplaatsen.

14. Als gebruiker wil ik dat de robot de vooraf geplande acties uitvoert en hier niet van afwijkt.

Er zitten in deze lijst van designkeuzes items die erg met elkaar overeenkomen of hetzelfde zijn. Daarom wordt punt 11 uit de lijst gehaald aangezien dit praktisch hetzelfde punt is als punt 4.

### Use cases

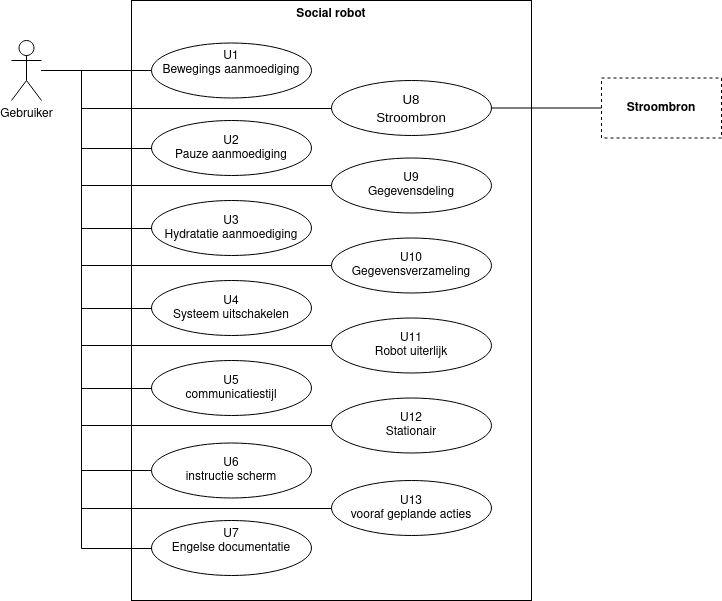
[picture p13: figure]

ID | U1
Naam | Bewegings aanmoediging
Actoren | Gebruiker, Robot
Samenvatting | De robot herinnert mensen om elk half uur minimaal 5 minuten te bewegen.
Precondities | 1. De robot is op een stroombron aangesloten. 2. De robot staat aan.
Scenario | 1. De robot laat een halfuur voorbijgaan en plaats

| dan een animatie op zijn scherm met daarop een lopend personage. 2. De robot maakt piepjes om aan te geven dat er iets op het scherm wordt getoond.
Postcondities | De gebruiker ziet dat de robot aanraadt om even te bewegen.
ID | U2
Naam | Pauze aanmoediging
Actoren | Gebruiker, Robot
Samenvatting | De robot herinnert mensen om elke 2 uur een pauze te nemen.
Precondities | 1. De robot is op een stroombron aangesloten. 2. De robot staat aan.
Scenario | 1. De robot laat 2 uur voorbijgaan en plaats dan een animatie op zijn scherm met daarop een animatie die een pauze indiceert. 2. De robot maakt piepjes om aan te geven dat er iets op het scherm wordt getoond.
Postcondities | De gebruiker ziet dat de robot aanraadt om pauze te nemen
ID | U3
Naam | Hydratatie aanmoediging
Actoren | Gebruiker, Robot
Samenvatting | De robot herinnert mensen om elk uur een glas water te drinken.
Precondities | 1. De robot is op een stroombron aangesloten. 2. De robot staat aan.
Scenario | 1. De robot laat een uur voorbijgaan en plaatst dan een animatie op zijn scherm met daarop een glas water. 2. De robot maakt piepjes om aan te geven dat er iets op het scherm wordt getoond.
Postcondities | De gebruiker ziet dat de robot aanraadt om een glas water te drinken.
ID | U4
Naam | Systeem uitschakelen

Actoren | Gebruiker, Robot
Samenvatting | De robot heeft een uit knop waarmee het systeem volledig uitgeschakeld wordt.
Precondities | 1. De robot is op een stroombron aangesloten.
Scenario | 1. De gebruiker haalt de stroomkabel van de robot los van de stroombron.
Postcondities | De robot staat uit.
ID | U5
Naam | Communicatiestijl
Actoren | Gebruiker, Robot
Samenvatting | De robot maakt gebruik van piepjes, beweging en afbeeldingen om te communiceren.
Precondities | 1. De robot is op een stroombron aangesloten. 2. De robot staat aan.
Scenario | 1. De robot laat iets op het scherm zien. 2. De robot maakt een piepje om aan te tonen dat de robot iets nieuws toont. 3. De robot maakt een paar bewegingen met het hoofd om aan te tonen dat de robot om de aandacht vraagt.
Postcondities | De gebruiker ziet dat de robot aanraadt om een glas water te drinken.
ID | U6
Naam | Instructie scherm
Actoren | Gebruiker, Robot
Samenvatting | De robot heeft een scherm waarop instructies kunnen worden getoond.
Precondities | 1. De robot is op een stroombron aangesloten. 2. De robot staat aan.
Scenario | 1. de robot bezit een scherm om animaties op te tonen. DIt zijn de notificatie animaties en het robot gezicht van de robot.
Postcondities | De gebruiker ziet wat de robot op het scherm aanduidt.
ID | U7

Naam | Engelse documentatie
Actoren | Gebruiker
Samenvatting | Alle documentatie rond het gebruik van de robot wordt in het engels geschreven.
Precondities | De Gebruiker heeft toegang tot de documentatie.
Scenario | De gebruiker leest de documentatie van de robot.
Postcondities | De gebruiker heeft de kennis uit de documentatie tot zich kunnen nemen.
ID | U8
Naam | Stroombron
Actoren | Gebruiker, Robot
Samenvatting | De robot wordt op een standaard USB-poort aangesloten voor stroom.
Precondities | De robot heeft een stroomkabel
Scenario | 1. De gebruiker sluit de robot aan met de kabel van de robot op een USB poort. 2. De robot ontvangt stroom en kan aangezet worden.
Postcondities | De robot kan aangezet worden.
ID | U9
Naam | Gegevensdeling
Actoren | Gebruiker, Robot
Samenvatting | De robot deelt geen gegevens met derde partijen.
Precondities | 1. De robot is op een stroombron aangesloten. 2. De robot staat aan.
Scenario | 1. Als de robot aangesloten wordt op een systeem moet eerst een wachtwoord worden ingevoerd. Dit wachtwoordt wordt met de documentatie van de robot meegeleverd. 2. De gebruiker voert het wachtwoord in. 3. a. wachtwoord: onjuist Er wordt opnieuw naar een wachtwoord gevraagd. b. wachtwoord: correct De gegevens van de robot worden naar het scherm geprint.
Postcondities | De gebruiker heeft wel of niet gegevens ontvangen van de robot.

ID | U10
Naam | Gegevensverzameling
Actoren | Robot
Samenvatting | De robot verzameld geen informatie over de gebruiker afgezien van wat de gebruiker de robot geeft.
Precondities | 1. De robot is op een stroombron aangesloten. 2. De robot staat aan.
Scenario | 1. De robot slaat geen sensor data op.
Postcondities | De robot heeft geen gegevens opgeslagen van de sensoren.
ID | U11
Naam | Robot uiterlijk
Actoren | Robot
Samenvatting | De robot heeft geen scherpe randen of puntige objecten. De robot is glad.

Precondities
Scenario | Het ontwerp van de robot bevat geen scherpe randen of punten.
Postcondities | Het ontwerp van de robot bevat geen scherpe randen of punten.
ID | U12
Naam | Stationair
Actoren | Robot
Samenvatting | De robot is stationair en kan niet zonder hulp van de gebruiker van locatie veranderen.
Precondities | 1. De robot is op een stroombron aangesloten. 2. De robot staat aan.
Scenario | De robot kan niet rijden of vooruitschuiven.
Postcondities | De robot staat op dezelfde plek.
ID | U13
Naam | Vooraf geplande acties
Actoren | Robot

Samenvatting | De robot voert altijd de vooraf geplande acties uit en wijkt hier niet van af.
Precondities | 1. De robot is op een stroombron aangesloten. 2. De robot staat aan.
Scenario | 1. De gebruiker interacteert met de robot of een getimed event vindt plaats. 2. De robot reageert op dit event zoals geprogrammeerd.
Postcondities | De robot heeft de correcte reactie op een event gegeven.

### MoSCoW

Om de verschillende use cases een prioriteit te geven is de MoSCoW methode toegepast. De use cases zijn ingedeeld op basis van afhankelijkheid van elkaar en overal belang. Er zijn geen use cases ingedeeld in de “Won’t haves” categorie aangezien uit het value sensitive design process geen onbelangrijke use cases zijn gekomen.

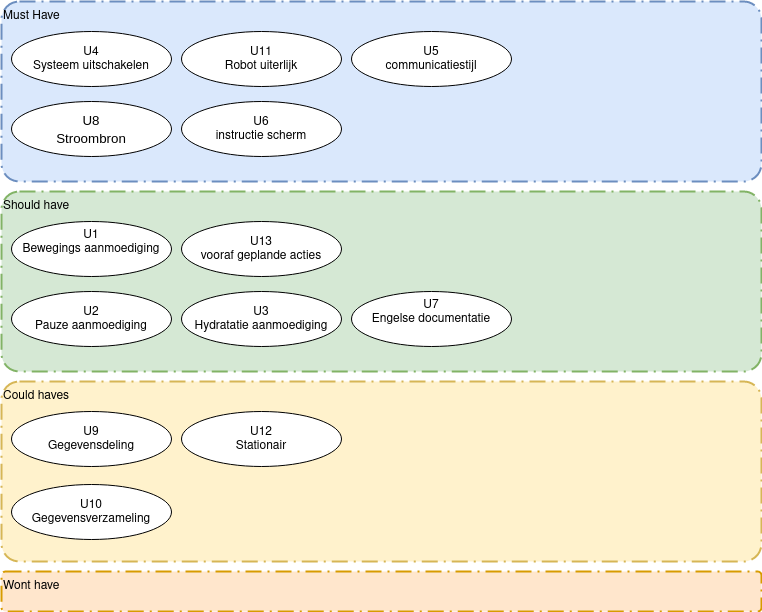
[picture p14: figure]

## Robot ontwerp

Met de gevonden design features wordt het basis robot ontwerp uitgebreid. De robot heeft met value sensitive design de volgende hardware aspecten opgedaan:

1. Een scherm voor een gezicht en animaties.
2. Een buzzer om geluid te kunnen maken met verschillende toonhoogten.
3. Een stroomkabel.

4. Een plaats om informatie binnen de robot op te slaan die niet gewist wordt als stroom verloren wordt.

Dit zijn de aspecten die uit stakeholders zijn gekomen maar ik wil vanuit mijzelf als programmeur nog een aantal aspecten toevoegen die ik vanuit de lijst van bestaande robots gevonden heb. Dit zijn het toevoegen van een bewegingssensor zodat de robot op een object kan focussen en hiernaar kan kijken. Om te kunnen kijken voeg ik 2 servo motors toe zodat een hoofd naar links en rechts en op en neer kan kijken. Dit zorgt ervoor dat er met de robot gespeeld kan worden.

Voor de bewegingssensor zijn er verschillende opties die kunnen worden geïmplementeerd. De keuze van de sensor heeft ook veel invloed op het uiteindelijke ontwerp van de robot aangezien de sensor aan de oppervlakte moet. er is gekozen voor een rode passive infrared sensor. Met deze use cases is het volgende ontwerp ontstaan:

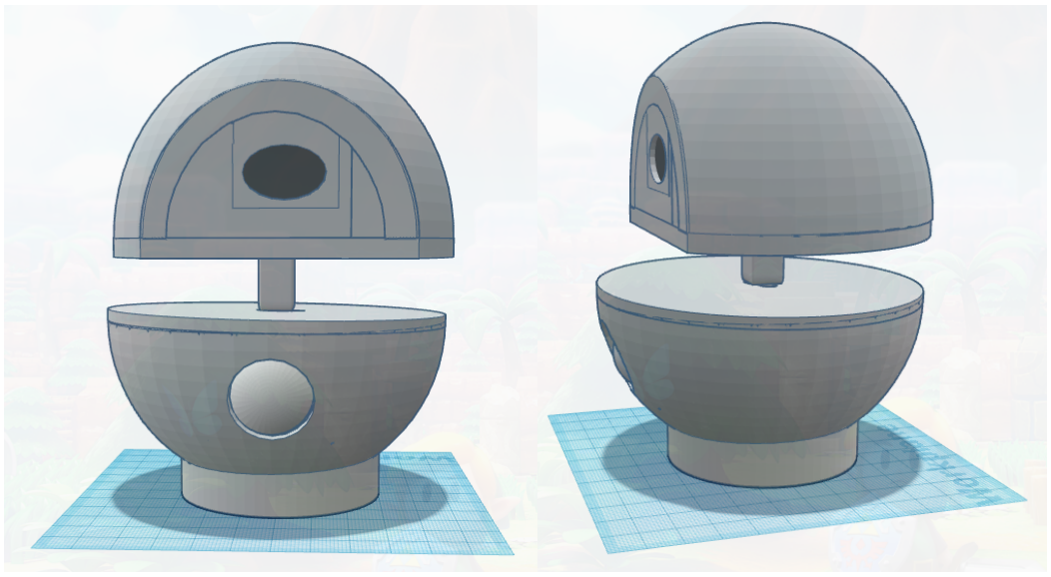
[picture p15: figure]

Dit ontwerp heeft een paar punten waarop verbeterd kan worden. Het verbindingsstuk tussen het “hoofd” en het “lijf” is erg dun en kan beschadigd raken. verder heeft de robot een gezicht wat vooruit gericht staat. dit zorgt ervoor dat de robot in standaard positie in het niks kijkt aangezien de robot redelijk kort is. Daarom is het ontwerp aangepast zodat de robot robuuster en vriendelijker is.

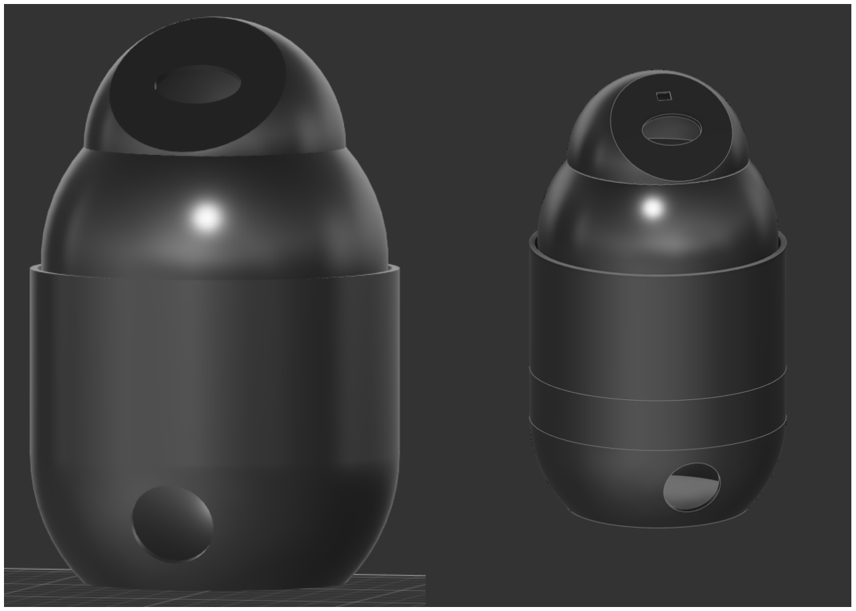
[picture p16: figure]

De basis voor deze robot is het gekomen uit het value sensitive design maar er is ook met technisch oog gekeken naar het ontwerp. Veel aspecten van de robot zijn aangepast om ruimte te maken voor hardware en bekabeling. Ook heeft de robot een bewegend aspect waardoor er rekening met beweging moest worden gehouden. Door middel van fysieke testen is het ontwerp verbeterd en geëvalueerd.

## Gezicht animaties

De robot heeft een klein zwart wit scherm om een gezicht te kunnen tonen en de gebruiker van bepaalde onderwerpen bewust te maken. Om een gezicht te ontwerpen voor deze robot is gekeken naar het paper “Characterizing the Design Space of Rendered Robot Faces” (Kalegina et al., 2018) waarin gekeken wordt naar de verschillende robot gezichten op schermen en hoe mensen hierop reageren. Uit dit onderzoek kwam naar voren dat robots zonder mond als eng worden gezien en dat ogen met irissen als vriendelijker worden gezien.

Gezichten zonder een mond werden gezien als het meest onvriendelijk. Om al deze punten mee te nemen is het volgende gezicht ontworpen. Er zijn animaties voor knipperen en een idle animatie om ervoor te zorgen dat de robot niet leeg in het niks staart. Verder zijn er ook animaties voor het kijken in de 4 verschillende hoeken van het scherm.

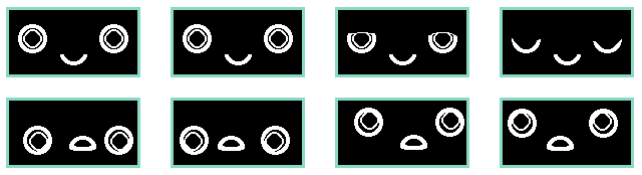
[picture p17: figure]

De idle animatie van de robot bestaat uit een kleine beweging van de ogen met een afwisselende knipper.

Om verschillende evenementen aan te geven zijn de volgende animaties gemaakt:

Herinnering om water te drinken

Herinnering om een pauze te nemen

Herinnering om een stukje te lopen

Als ik deze robot op het framework van Friedman, B., Kahn, P. H., Borning, A., & Zhang, P neerleg krijg de robot een score van ongeveer 6. De robot is niet volledig autonoom maar geeft hier wel de indruk van.
framework: form | Framework: modality | framework: social norms | framework: autonomy | framework: interactivity
abstract | audio, visueel, beweging | De robot heeft een lichtelijke kennis van menselijke behoefte zoals het aantal nodige pauzes op een dag. | De robot heeft een paar autonome aspecten maar wordt nog bestuurd door een vast programma. | De robot is zich bewust van beweging in zijn omgeving en kan hiermee interacteren.

## Robot naamgeving

De ontworpen desktop companion moet een naam krijgen om hem als product te kunnen gebruiken. Een overweldigende groep aan bestaande robots hebben korte en krachtige namen als “Buddy”, “Tito” en “PIA”. Deze kortere namen zorgen ervoor dat de robot beter onthouden wordt en dat er makkelijk over gepraat kan worden. Daarom krijgt de desk companion robot een korte naam bestaande uit een afkorting. De kerndoelen van deze robot zijn:

1. Het zijn van een companion of een deskpet.
2. Het makkelijk programmeerbaar zijn om te kunnen testen en onderzoeken met de robot.

Met deze ideeën is een woordweb gemaakt waar een paar opties uit zijn gekomen:

1. ROCO, Robot Companion.
2. DECO, Desktop Companion.
3. PRODECO, Programmable Desktop Companion.
4. HAROCO, Health Assistant Robot Companion.

De robot krijgt de naam DECO, Desktop Companion aangezien een korte krachtige naam beter blijft hangen bij de gebruiker. Deze naam is voorgelegd bij een aantal directe stakeholders die positief reageerden op de naamgeving.

## Bronnen

Bartneck, C., & Forlizzi, J. (2004). A Design-Centred Framework for Social Human-Robot Interaction.

591-594.

Cheon, E., & Makoto Su, N. (n.d.). Integrating Roboticist Values into aValue Sensitive Design

Framework for Humanoid Robots.

https://www.researchgate.net/profile/Eunjeong_Cheon/publication/301912963_Integrating_roboti

cist_values_into_a_design_framework_for_humanoid_robots/links/5ca040e8299bf11169521a33/I

ntegrating-roboticist-values-into-a-design-framework-for-humanoid-robots.pdf

Friedman, B., Kahn, P. H., Borning, A., & Zhang, P. (2006). Value Sensitive Design and Information

Systems. M. E. Sharpe.

https://www.researchgate.net/publication/229068326_Value_Sensitive_Design_and_Information_

Systems

Kalegina, A., Berlin, K., Schroeder, G., Cakmak, M., & Allchin, A. (2018, Maart 5-8). Characterizing the

Design Space of Rendered Robot Faces. Characterizing the Design Space of Rendered Robot

Faces, 1(Robot faces), 1-0. https://par.nsf.gov/servlets/purl/10067196

Rijksinstituut voor Volksgezondheid en Milieu. (2018, Oktober 19-10-2018). Zitgedrag.

www.sportenbewegenincijfers.nl.

https://www.sportenbewegenincijfers.nl/kernindicatoren/zitgedrag

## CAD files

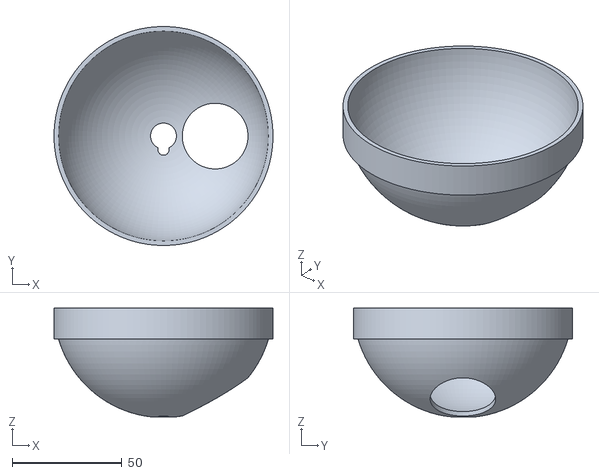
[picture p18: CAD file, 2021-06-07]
3DPrint/Extra_STL/upper_body.stl
100.0 x 100.0 x 49.7

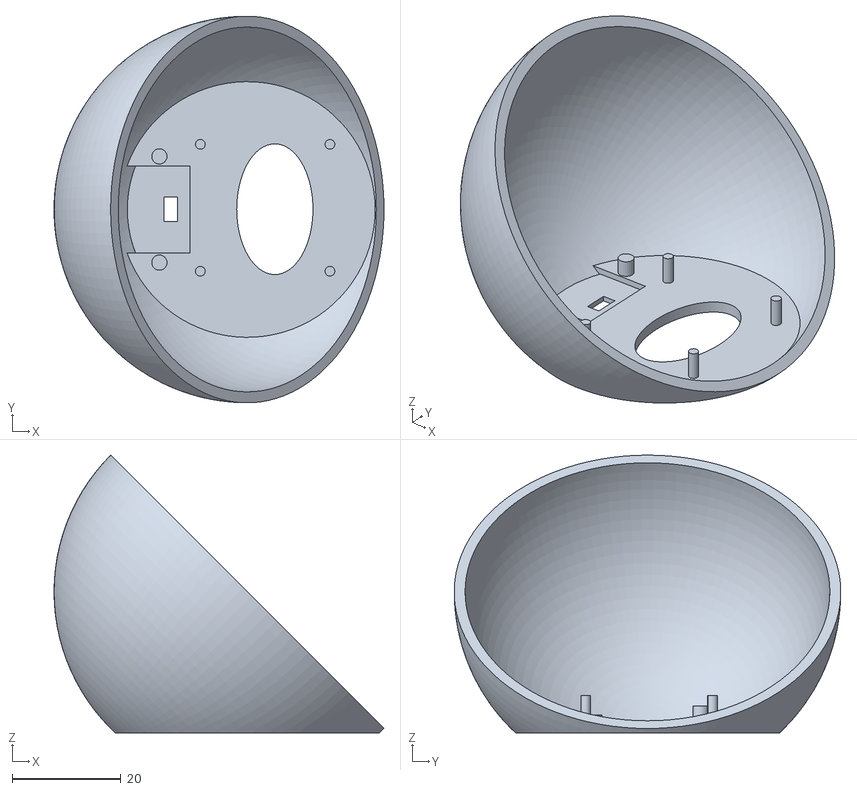
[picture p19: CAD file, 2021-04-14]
3DPrint/upper_head_oled_lidar.stl
60.6 x 71.0 x 51.0

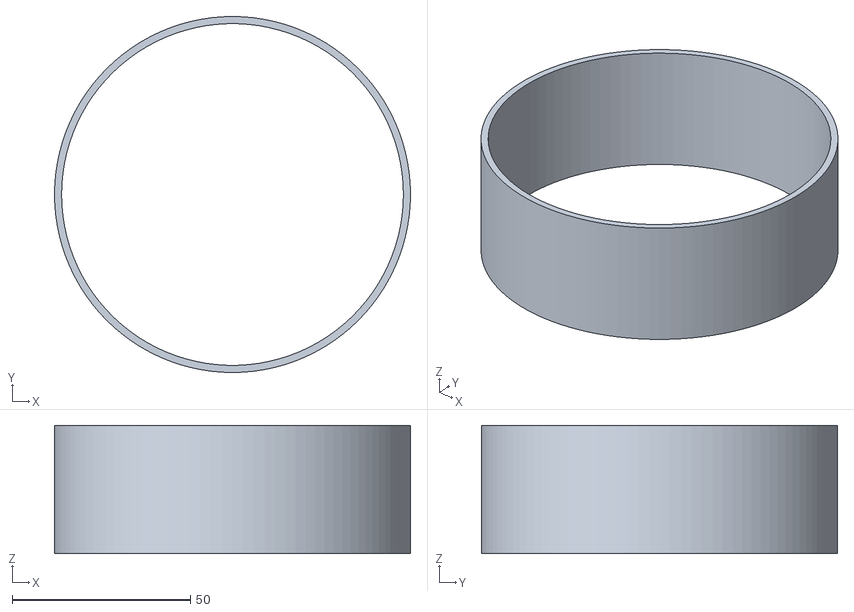
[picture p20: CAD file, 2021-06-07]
3DPrint/Extra_STL/middle_body.stl
100.0 x 100.0 x 36.0

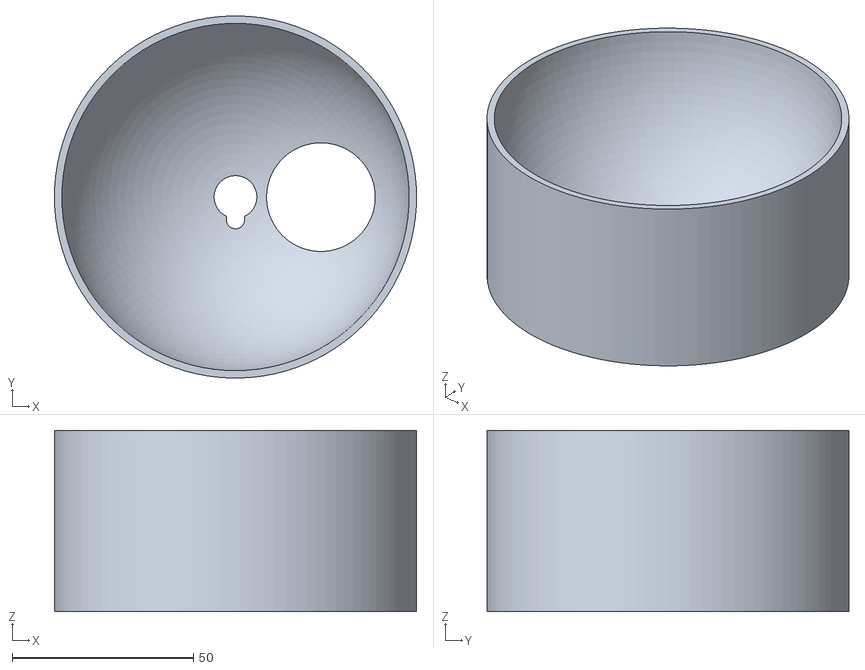
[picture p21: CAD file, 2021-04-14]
3DPrint/upper_body.stl
100.0 x 100.0 x 50.0

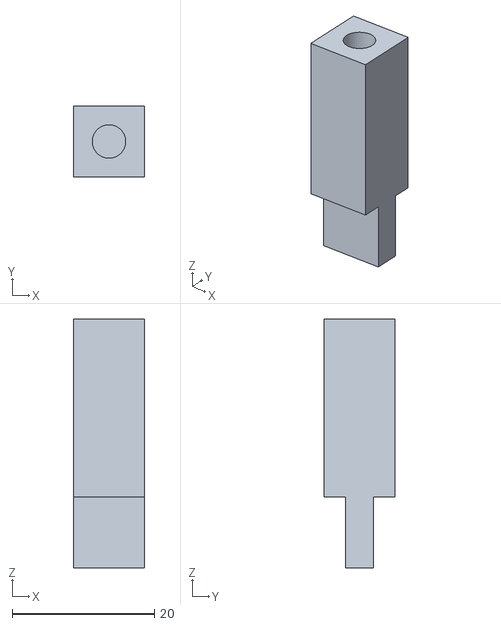
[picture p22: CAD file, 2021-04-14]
3DPrint/neck_vertical.stl
10.0 x 10.0 x 35.0

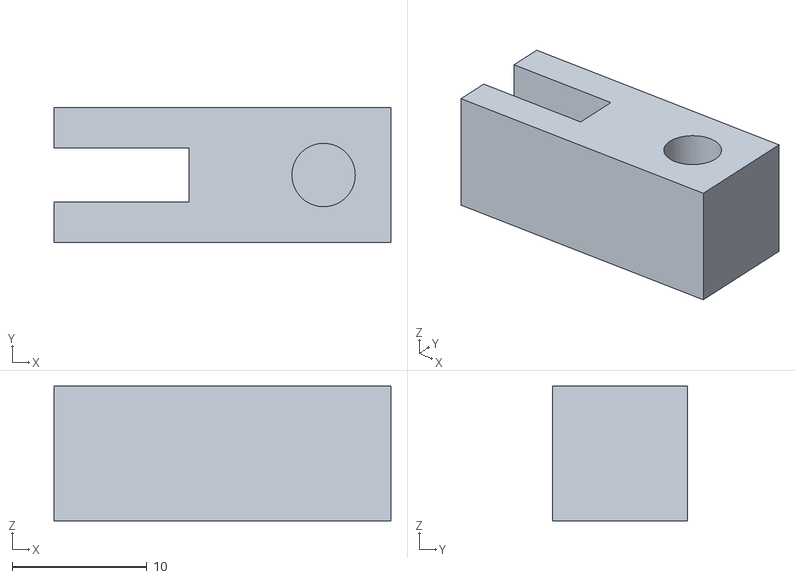
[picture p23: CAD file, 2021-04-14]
3DPrint/neck_horizonal.stl
25.0 x 10.0 x 10.0

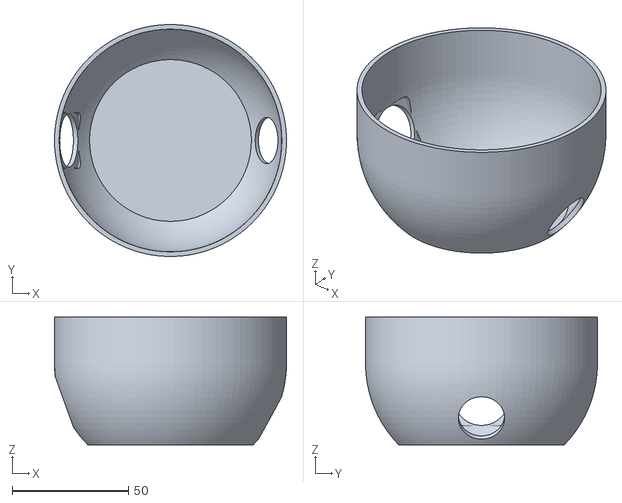
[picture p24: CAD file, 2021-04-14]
3DPrint/lower_body.stl
100.0 x 100.0 x 55.0

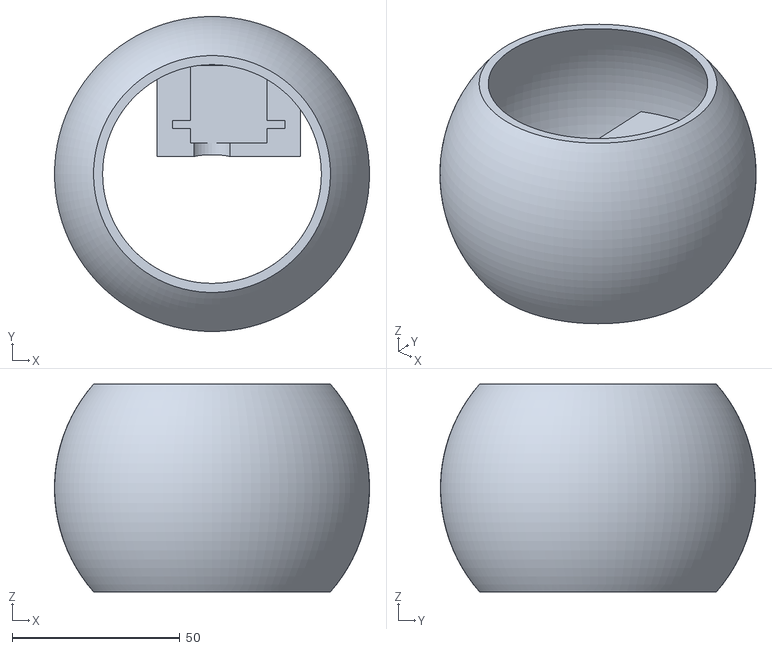
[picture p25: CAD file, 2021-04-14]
3DPrint/lower_head.stl
94.0 x 94.0 x 62.0

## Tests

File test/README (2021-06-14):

This directory is intended for PlatformIO Unit Testing and project tests.

This project does not contain unit tests, This project heas been tested with the code in test_scripts.txt and all commands have been tested using REPL

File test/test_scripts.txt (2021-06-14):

Some of the run test scripts used to determine if the interpreter is functional

test for IntegerNode and MAthNode:
SETUP:
    x = 3
    y = 4
    x + y 

    x = 3
    y = 4
    x - y

    x = 3
    y = 4
    x * y

    x = 3
    y = 4
    x / y

    a = 3
    b = a 

    b + a
EOF:
results:
7, -1, 12, 0, a = 3, b = 3, 6

SetterNode tests:

SETUP:
    weatherstation = NON_ACTIVE
    walk_reminder = NON_ACTIVE
    weatherstation = NON_ACTIVE
    break_reminder = NON_ACTIVE

    weatherstation = ACTIVE
    walk_reminder = ACTIVE
    weatherstation = ACTIVE
    break_reminder = ACTIVE
 
    STATE = IDLE
    STATE = REMINDER_BREAK
    STATE = REMINDER_WATER
    STATE = REMINDER_WALK
    STATE = WEATHER_STATION
    STATE = INTERACTIVE_MODE
    STATE = OFF  

    STATE = IDLE

    shut_down_after = 10 MILLI_SECOND
    shut_down_after = 10 SECOND
    shut_down_after = 1 MINUTE
    shut_down_after = 1 HOUR

    weatherstation DURATION = 1 MINUTE
    walk_reminder DURATION = 1 MINUTE
    weatherstation DURATION = 1 MINUTE
    break_reminder DURATION = 1 MINUTE

    weatherstation PERIOD = 1 MINUTE
    walk_reminder PERIOD = 1 MINUTE
    weatherstation PERIOD = 1 MINUTE
    break_reminder PERIOD = 1 MINUTE

    interactive_mode DURATION = 2 MINUTE
LOOP:
EOF:

Test voor setters  
SETUP:
    getBreakTime
    getWalkTime
    getWaterTime
    getWeatherStationTime
    getState
    getHeadPos
    getNeckPos
EOF:

SETUP:
    x = 180
    move_head x
    move_neck x
EOF:

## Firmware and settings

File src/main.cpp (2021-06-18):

// Copyright (C) 2021  Maaike Hovenkamp

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
#include "robot_interpreter.hpp"

rtos::Thread servo_task;
rtos::Thread pir_task;
rtos::Thread robot_task;
rtos::Thread robot_control_task;
rtos::Thread i2c_task;
rtos::Thread animation_task;

PIRSensor pir_sensor(2);
Servo neck_servo(3);
Servo head_servo(4);
MicroLidar lidar;
OledScreen screen;
Robot robot_test(head_servo,neck_servo,pir_sensor,lidar,screen,5);
ServoPositions servo_positions;
Interpreter interpreter(robot_test);

ROBOT_STATES global_state;

/**
 * @brief i2c task, responsible for the oled and lidar i2c communication. 
 * 
 */
void i2cTask(){
  Serial.println("i2c task started");
  while(true){
    if( global_state != ROBOT_STATES::OFF ){
      screen.flashOled();
      lidar.lidarTask();
    }
    rtos::ThisThread::sleep_for(MS(150));
  }
}

void animationTask(){
  Serial.println("animation task started");
  while(true){
    screen.showAnimation();
  }
}

/**
 * @brief servoTask, continues loop supporting the head and neck servo of the robot.
 * 
 */
void servoTask(){
  Serial.println("servo head task started");
  while(true){
    if( global_state != ROBOT_STATES::OFF ){
      neck_servo.servoTask();
      head_servo.servoTask();
      rtos::ThisThread::sleep_for(MS(20)); // 20 ms standard for sg932r TowerPro, change when changing servo
    }
  }
}


/**
 * @brief PIRTask, continues loop that polls the PIR sensor.
 * 
 */
void pirTask(){
  Serial.println("PIR task started");
  while(true){ 
    pir_sensor.PIRTask();
    rtos::ThisThread::sleep_for(MS(1000));
  }
}

/**
 * @brief robotTask, continues loop runnning the robot.
 * 
 */
void robotTask(){
  Serial.println("main robot task started");
  while(true){
    robot_test.run();
  }
}

/**
 * @brief robotControlTask, continues loop running the control of the user over the robot.
 * 
 */
void robotControlTask(){
  Serial.println("robot control task started");
  delay(5000);
  while (true){
    interpreter.run();
  }
}

/**
 * @brief setup function containing the strat of the threads. 
 * 
 */
void setup(){


  Serial.begin(9600);
  delay(2000);
  robot_test.setup();
  
  Serial.println("==========================================================================");
  Serial.println("DECO  Copyright (C) 2021  Maaike Hovenkamp");
  Serial.println("This program comes with ABSOLUTELY NO WARRANTY; for details type");
  Serial.println("This is free software, and you are welcome to redistribute it");
  Serial.println("==========================================================================");

  osStatus error;
  error = pir_task.start(pirTask);
  if(error){Serial.println(error);}

  error = robot_control_task.start(robotControlTask);
  if(error){Serial.println(error);}
  error = robot_task.start(robotTask);
  if(error){Serial.println(error);}
  error = i2c_task.start(i2cTask);
  if(error){Serial.println(error);}
  error = animation_task.start(animationTask);
  if(error){Serial.println(error);}
  
  //wait till servos are at 90 degrees before starting the task
  while(neck_servo.getCurrentDegree() != 90 && head_servo.getCurrentDegree() != 90){}
  error = servo_task.start(servoTask);
  if(error){Serial.println(error);}
};


/**
 * @brief loop function not in use due to use of MBED OS.
 * 
 */
void loop(){}

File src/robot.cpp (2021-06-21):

#include "../include/robot.hpp"

extern ROBOT_STATES global_state;

void Robot::setup(){
    Serial.println("---start setup robot---");
    // setup al peripherals
    internal_sensors.setup();
    face_screen.setup();
    lidar.setup();
    rtos::ThisThread::sleep_for(MS(1000)); // give time for i2C to get ready
    head_servo.setup();
    neck_servo.setup();
    // returnToStartPos();
    rtos::ThisThread::sleep_for(MS(2000)); // give time for servo's to move to strat position
    // play startup sound
    Songs songs;
    playSound<songs.start_up.size()>(songs.start_up);
    // seperate timers for each timed event
    start_time_timer_water = millis();
    start_time_timer_walk = millis();
    start_time_timer_break = millis();
    start_time_timer_weather = millis();
    // set states to IDLE to start robot
    current_state = ROBOT_STATES::IDLE;
    prev_state = ROBOT_STATES::IDLE;
    temp_state = ROBOT_STATES::IDLE;
    Serial.println("---finished setup robot---");
};

void Robot::run(){
    if( pir_sensor.getLastMovement() >= 1200){ //after 20 minutes of no activity shut down.
        setState(ROBOT_STATES::OFF);
    }
    if( current_state != ROBOT_STATES::OFF){ // Check timers for timed actions
        if( millis() - start_time_timer_water >=  getWaterTime()){
            setState(ROBOT_STATES::REMINDER_WATER);
            start_time_timer_water = millis();
        } else if( millis() - start_time_timer_walk >=  getWalkTime()){
            setState(ROBOT_STATES::REMINDER_WALK);
            start_time_timer_walk = millis();
        } else if( millis() - start_time_timer_break >=  getBreakTime()){
            setState(ROBOT_STATES::REMINDER_BREAK);
            start_time_timer_break = millis();
        } else if( millis() - start_time_timer_weather >=  getWeatherStationTime()){
            setState(ROBOT_STATES::WEATHER_STATION);
            start_time_timer_weather = millis();
        }
    } else {
        start_time_timer_water = millis();
        start_time_timer_walk = millis();
        start_time_timer_break = millis();
        start_time_timer_weather = millis();
    }
    switch(current_state){
        case ROBOT_STATES::INTERACTIVE_MODE:
            interactiveMode();
            break;
        case ROBOT_STATES::IDLE:
            idleState();
            break;
        case ROBOT_STATES::REMINDER_BREAK:
            if(break_time_active){
                reminderBreak();
            } else {
                setState(prev_state);
            }
            break;
        case ROBOT_STATES::REMINDER_WATER:
            if(water_time_active){
                reminderWater();
            } else {
                setState(prev_state);
            }
            break;
        case ROBOT_STATES::REMINDER_WALK:
            if(walk_time_active){
                reminderWalk();
            } else { 
                setState(prev_state);
            }
            break;
        case ROBOT_STATES::WEATHER_STATION:
            if(weather_time_active){
                showWeatherStation();
            } else {
                setState(prev_state);
            }
            break;
        case ROBOT_STATES::OFF:
            shutDown();
            break;
        default:
            break;
    }
    rtos::ThisThread::sleep_for(MS(100));
};

unsigned int Robot::getBreakTime(){
    return break_time;
}
unsigned int Robot::getWalkTime(){
    return walk_time;
}
unsigned int Robot::getWaterTime(){
    return water_time;
}
unsigned int Robot::getWeatherStationTime(){
    return weather_station_time;
}
unsigned int Robot::getMicroLidarDistance(){
    return lidar.getDistanceMM();
}

void Robot::setBreakTimeActive(bool active){
    break_time_active = active;
}
void Robot::setWalkTimeActive(bool active){
    walk_time_active = active;
}
void Robot::setWaterTimeActive(bool active){
    water_time_active = active;
}
void Robot::setWeatherStationActive(bool active){
    weather_time_active = active;
}

void Robot::setBreakTime(unsigned long time){
    break_time = time;
}
void Robot::setWalkTime(unsigned long time){
    break_time = time;
}
void Robot::setWaterTime(unsigned long time){
    break_time = time;
}
void Robot::setShutdownAfter(unsigned long time){
    shutdown_after = time;
}
void Robot::setWeatherStationTime(unsigned long time){
    weather_station_time = time;
}

void Robot::setBreakTimeDuration(unsigned long time){
    break_time_duration = time;
}
void Robot::setWalkTimeDuration(unsigned long time){
    walk_time_duration = time;
}
void Robot::setWaterTimeDuration(unsigned long time){
    water_time_duration = time;
}
void Robot::setInteractiveModeDuration(unsigned long time){
    interactive_mode_duration = time;
}
void Robot::setWeatherStationDuration(unsigned long time){
    weather_station_duration = time;
}


void Robot::setState(ROBOT_STATES state){ // prev = IDLE temp = WEATHER current = WEATHER
    temp_state = current_state;
    current_state = state;
    if( temp_state != current_state){ // state change
        prev_state = temp_state;
    }
};
ROBOT_STATES Robot::getState(){
    return current_state;
};
void Robot::printState(ROBOT_STATES state_to_print){
    switch (state_to_print){
        case ROBOT_STATES::IDLE:
            Serial.println("IDLE");
            break;
        case ROBOT_STATES::INTERACTIVE_MODE:
            Serial.println("INTERACTIVE_MODE");
            break;
        case ROBOT_STATES::OFF:
            Serial.println("OFF");
            break;
        case ROBOT_STATES::REMINDER_BREAK:
            Serial.println("REMINDER_BREAK");
            break;
        case ROBOT_STATES::REMINDER_WALK:
            Serial.println("REMINDER_WALK");
            break;
        case ROBOT_STATES::REMINDER_WATER:
            Serial.println("REMINDER_WATER");
            break;
        case ROBOT_STATES::WEATHER_STATION:
            Serial.println("WEATHER_STATION");
            break;
        default:
            break;
        }
}

void Robot::moveHead( int pos ){
    int max_turn_up = 140;
    int max_turn_down = 40;
    if( pos >= max_turn_up){
        pos = max_turn_up;
    }
    if( pos <= max_turn_down){
        pos = max_turn_down;
    }
    head_servo.turnToDegree(pos);
};
void Robot::moveNeck( int pos ){
    neck_servo.turnToDegree(pos);
};

int Robot::getHeadPos(){
    return head_servo.getCurrentDegree();
}
int Robot::getNeckPos(){
    return neck_servo.getCurrentDegree();
}

int Robot::getLastMovementDetected(){
    return pir_sensor.getLastMovement();
}



void Robot::shutDown(){
    returnToStartPos();
    global_state = ROBOT_STATES::OFF;
    face_screen.clearScreen();
    Serial.println("shutdown acitve");
    while(pir_sensor.getLastMovement() >= shutdown_after){
        rtos::ThisThread::sleep_for(MS(500));
    }
    Serial.println("restart");
    global_state = ROBOT_STATES::IDLE;
    setState(ROBOT_STATES::IDLE);
};
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

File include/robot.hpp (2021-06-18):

// ==========================================================================
// robot.hpp
// Copyright (C) 2021  Maaike Hovenkamp

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
# ifndef ROBOT_HPP
# define ROBOT_HPP

#include "servo.hpp"
#include "PIRsensor.hpp"
#include "oledScreen.hpp"
#include "internalBleSensors.hpp" 
#include "buzzer.hpp"
#include "microLidar.hpp"

/**
 * @brief enum class ROBOT_STATES, all posible robot states
 * 
 */
enum class ROBOT_STATES{
    IDLE,
    REMINDER_BREAK,
    REMINDER_WATER,
    REMINDER_WALK,
    WEATHER_STATION,
    INTERACTIVE_MODE,
    OFF
};

/**
 * @brief main Robot class supporting the social robotics robot.
 * 
 */
class Robot{
private:
    Servo &head_servo;
    Servo &neck_servo;
    PIRSensor &pir_sensor;
    MicroLidar &lidar;
    InternalBLESensors internal_sensors;
    OledScreen &face_screen;
    Buzzer buzzer;

    unsigned int break_time = 2 * HOUR;
    unsigned int walk_time = 30 * MINUTE;
    unsigned int water_time = 50 * HOUR;
    unsigned int shutdown_after = 5 * MINUTE;
    unsigned int weather_station_time = 5 * MINUTE;

    unsigned int break_time_duration = 15 * MINUTE;
    unsigned int walk_time_duration = 5 * MINUTE;
    unsigned int water_time_duration = 30 * SECOND;
    unsigned int interactive_mode_duration = 20 * SECOND;
    unsigned int weather_station_duration = 5 * SECOND;

    bool break_time_active = true;
    bool walk_time_active = true;
    bool water_time_active = true;
    bool weather_time_active = true;

    unsigned long start_time_timer_water;
    unsigned long start_time_timer_walk;
    unsigned long start_time_timer_break;
    unsigned long start_time_timer_weather;
    unsigned long current_time_difference;

    ROBOT_STATES current_state;
    ROBOT_STATES prev_state;
    ROBOT_STATES temp_state;

    unsigned int distance_found_object;
    unsigned int found_object_x;
    unsigned int found_object_y;
    unsigned int tmp_x_coordinate;
    unsigned int tmp_y_coordinate;
    

    /**
     * @brief tries to follow a found object by making a spiraling motion when hand is removed. 
     * 
     * @return true 
     * @return false 
     */
    bool followClosestObject();

    /**
     * @brief Idle state of the robot; idle animation.
     * 
     */
    void idleState();
    /**
     * @brief Break reminder state of the robot; attention movement, break animation
     * 
     */
    void reminderBreak();
    /**
     * @brief Walk reminder state of the robot; attention movement, notification, walk animation
     * 
     */
    void reminderWalk();
    /**
     * @brief Water reminder state of the robot; attention movement, notification, water animation
     * 
     */
    void reminderWater();
    /**
     * @brief Weather station state of the robot; weatherStation animation
     * 
     */
    void showWeatherStation();
    /**
     * @brief Makes the robot search out the user and look at hiim/follow him, return true after succes.
     * 
     * @return true 
     * @return false 
     */
    bool interactiveMode();
public:
    /**
     * @brief Construct a new Robot object
     * 
     * @param head_servo : Servo
     * @param neck_servo : Servo
     * @param pir_sensor : PIRSensor
     * @param lidar : MicroLidar
     * @param buzzer_pin : Buzzer
     */
    Robot(  Servo & head_servo,
            Servo & neck_servo,
            PIRSensor & pir_sensor,
            MicroLidar & lidar,
            OledScreen & face_screen,
            int buzzer_pin ):
            head_servo(head_servo),
            neck_servo(neck_servo),
            pir_sensor(pir_sensor),
            lidar(lidar),
            face_screen(face_screen),
            buzzer( Buzzer(buzzer_pin) )
        {}
    /**
     * @brief setup the robot, call before use of other functions
     * 
     */
    void setup();

    /**
     * @brief main run function of the robot
     * 
     */
    void run();


    /**
     * @brief Get the Break Time loop interval
     * 
     * @return unsigned int 
     */
    unsigned int getBreakTime();
    /**
     * @brief Get the Walk Time loop interval
     * 
     * @return unsigned int 
     */
    unsigned int getWalkTime();
    /**
     * @brief Get the Water Time loop interval
     * 
     * @return unsigned int 
     */
    unsigned int getWaterTime();
    /**
     * @brief Get the Weather Station Time object
     * 
     * @return unsigned int 
     */
    unsigned int getWeatherStationTime();

    /**
     * @brief Get the distance measured from the micro lidar in the head in mm
     * 
     * @return unsigned int 
     */
    unsigned int getMicroLidarDistance();

    /**
     * @brief Set the Break Time Active object
     * 
     * @param active 
     */
    void setBreakTimeActive(bool active);
    /**
     * @brief Set the Walk Time Active object
     * 
     * @param active 
     */
    void setWalkTimeActive(bool active);
    /**
     * @brief Set the Water Time Active object
     * 
     * @param active 
     */
    void setWaterTimeActive(bool active);
    /**
     * @brief Set the Break Time Active object
     * 
     * @param active 
     */
    void setWeatherStationActive(bool active);

    /**
     * @brief Set the Break Time loop interval
     * 
     * @param time : unsigned long, loop interval
     */
    void setBreakTime(unsigned long time);
    /**
     * @brief Set the Walk Time loop interval
     * 
     * @param time : unsigned long, loop interval
     */
    void setWalkTime(unsigned long time);
    /**
     * @brief Set the Water Time loop interval
     * 
     * @param time : unsinged long, loop interal
     */
    void setWaterTime(unsigned long time);
    /**
     * @brief Set the Shutdown After loop interval
     * 
     * @param time : unsigned long, shut down after x time of inactivity. 
     */
    void setShutdownAfter(unsigned long time);
    /**
     * @brief Set the Weather station Time loop interval
     * 
     * @param time 
     */
    void setWeatherStationTime(unsigned long time);

    /**
     * @brief Set the Break Time Duration 
     * 
     * @param time : unsinged long
     */
    void setBreakTimeDuration(unsigned long time);
    /**
     * @brief Set the Walk Time Duration 
     * 
     * @param time : unsigned long
     */
    void setWalkTimeDuration(unsigned long time);
    /**
     * @brief Set the Water Time Duration 
     * 
     * @param time : unsigned long
     */
    void setWaterTimeDuration(unsigned long time);
    /**
     * @brief Set the Interactive Mode Duration 
     * 
     * @param time : unsigned long
     */
    void setInteractiveModeDuration(unsigned long time);
    /**
     * @brief Set the Weather Station Duration
     * 
     * @param time 
     */
    void setWeatherStationDuration(unsigned long time);
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

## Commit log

2021-02-18 added servo and PIR classes, functional
2021-02-22 servos and pir working with embed OS
    [Hardware_model.fzz]
2021-03-01 working oled screen drivers and animation support
2021-03-02 memory mistake solved and added new face animations
    [main.cpp, oledScreen.hpp]
2021-03-03 added buzzer support, chords not correct
    [main.cpp]
2021-03-08 threads fully supported and main control robot functional
2021-03-17 fixed servo isues and rng movement state
    [main.cpp, oledScreen.hpp, robot.cpp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]
2021-03-19 buzzer fixed, timed events fixed, new animations for walk and break
    [main.cpp, robot.cpp, robot.hpp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]
2021-03-22 working on documentation push to push image
    [Hardware_model.fzz]
2021-03-30 added first support for sonar implementation
2021-04-01 first start on lexer and parser for individual language
    [Hardware_model.fzz]
2021-04-06 fisrt test with micro lidar bbut mbed os nto starting all tasks
2021-04-07 fixed embed os problem, first tests on lidar current problem: error code 8191
    [main.cpp, robot.cpp, robot.hpp]
2021-04-14 created folder for 3d prints
2021-04-14 added 3D print files
    [lower_body.stl, lower_head.stl, neck_horizonal.stl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]
2021-04-14 debugging sonar, todo:mutex
2021-04-16 fixed oled ticking and scheudling issues. pretty good process
    [main.cpp, oledScreen.hpp, robot.cpp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]
2021-04-20 added threads together and tested it
2021-04-26 executes for nodes and parser written, current issue: node execute purely virtual
    [robot.cpp, robot.hpp]
2021-05-10 working on file implementation, current issue: serial readString garbage letters
    [main.cpp, robot_interpreter.cpp]
2021-05-12 currrent issue TODO robot_interpreter.cpp
    [robot_interpreter.cpp]
2021-05-19 file functional, repl currently not.
2021-05-20 fixed file and repl implementation, aut inbuild code start and timing issues
    [main.cpp, robot.cpp, robot_interpreter.cpp]
2021-05-21 fixed walk reminder issue and some timing in interactive_mode
    [main.cpp, oledScreen.hpp, robot.cpp]
2021-05-26 fixed IDLE issue, added animation thread to speed up interactive mode
    [main.cpp, robot.cpp, robot.hpp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]
2021-05-27 Updates to robot code, small details like correct functions for servo motors.
    [main.cpp, robot.cpp, robot.hpp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]
2021-06-03 If statements functional error class updated in use and line_numbers added, demo load in preprogrammed
    [main.cpp, robot_interpreter.cpp]
2021-06-07 Extra files for print dificulty
    [middle_body.stl, upper_body.stl]
2021-06-09 Current issue, while loop sudden stop
    [robot_interpreter.cpp]
2021-06-18 changed servo speed
